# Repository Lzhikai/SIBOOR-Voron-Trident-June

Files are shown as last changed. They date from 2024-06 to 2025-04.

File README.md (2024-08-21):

## To improve readability, the assembly and debugging guides for the Trident JUNE have been gradually migrated to [https://docs.siboor.com/](https://docs.siboor.com/).

## The `printer.cfg` was updated on August 20:
1. Fixed the issue with excessively high maximum speed values.
2. Corrected the issue with excessively low maximum acceleration values.
3. Reversed the direction of the extruder motor.
4. Rewrote all fan configurations to allow separate activation and control of the FumePack filter module and additional part cooling fans in slicing.
5. Reduced the speed of the `z_tilt` operation.
6. Rewrote the macros for starting and ending prints.
7. Removed the Cartographer model to prevent users from homing without calibrating Cartographer.

# SIBOOR-Voron-Trident-June  

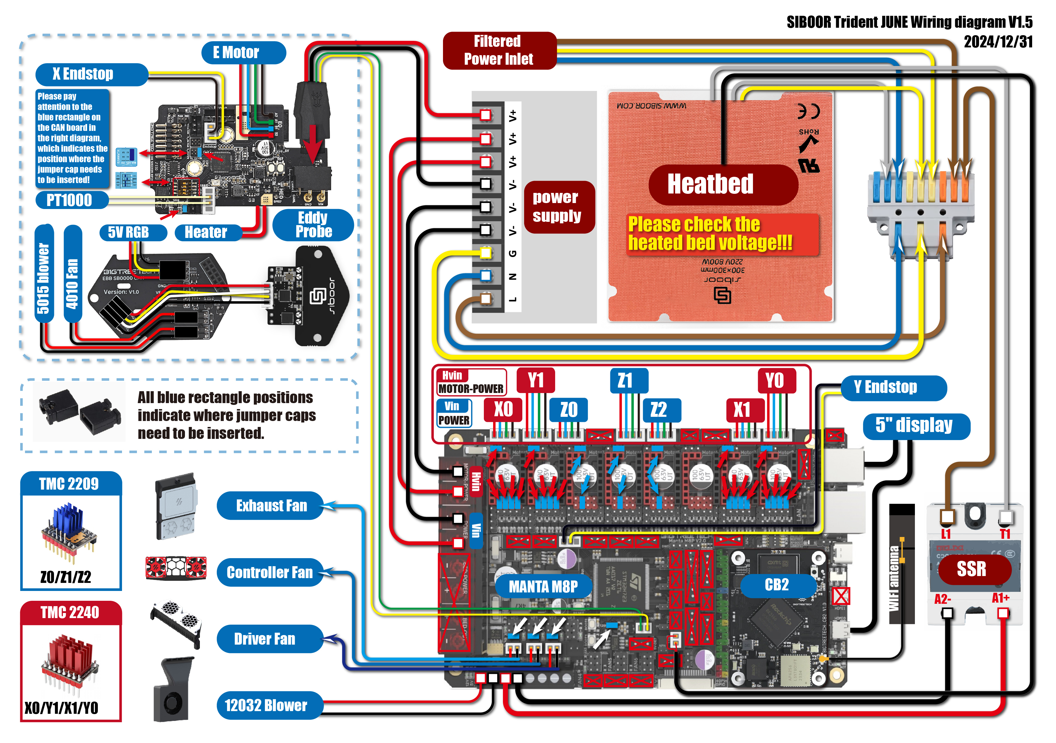
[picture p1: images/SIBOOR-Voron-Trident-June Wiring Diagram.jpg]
  

### SIBOOR-Voron-Trident-June  [BOM](https://github.com/Lzhikai/SIBOOR-Voron-Trident-June/blob/main/SIBOOR_Trident_%5BJUNE_2024%5D_BOM.md)
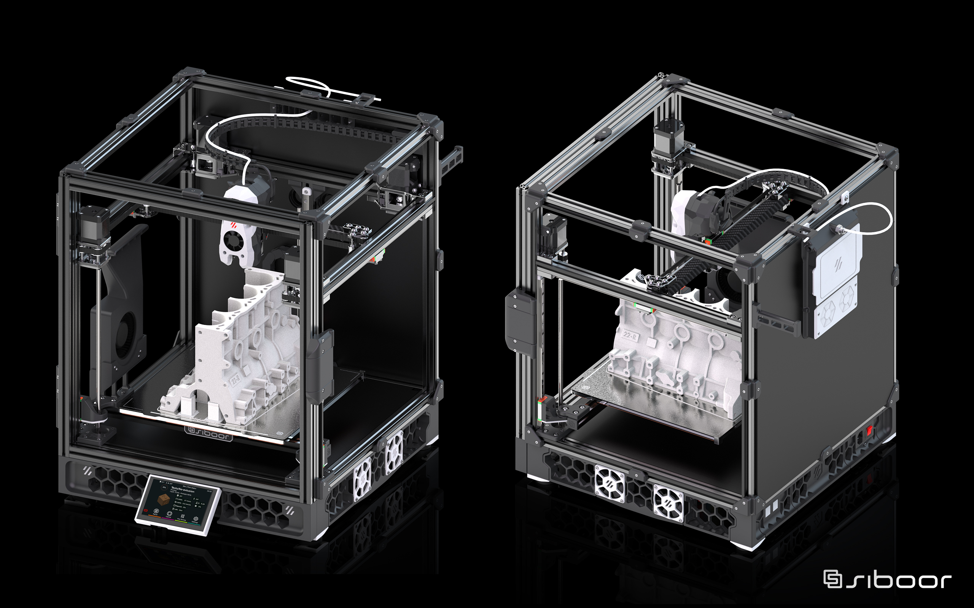
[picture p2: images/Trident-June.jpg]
  
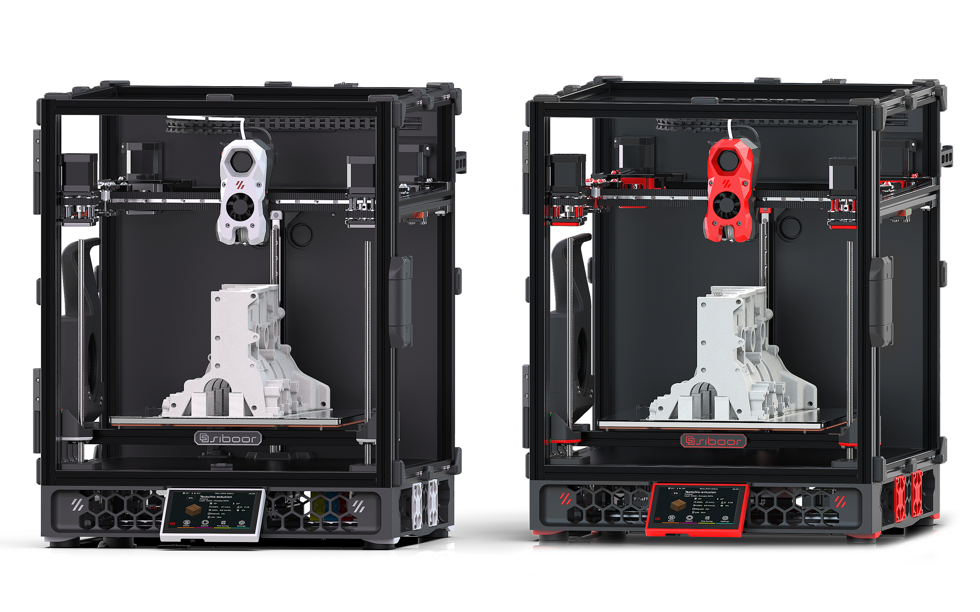
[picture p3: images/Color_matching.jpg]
  
# <p align="center"> 《CNC AWD metal parts schematic diagram》</p>    
  
<p align="center" >
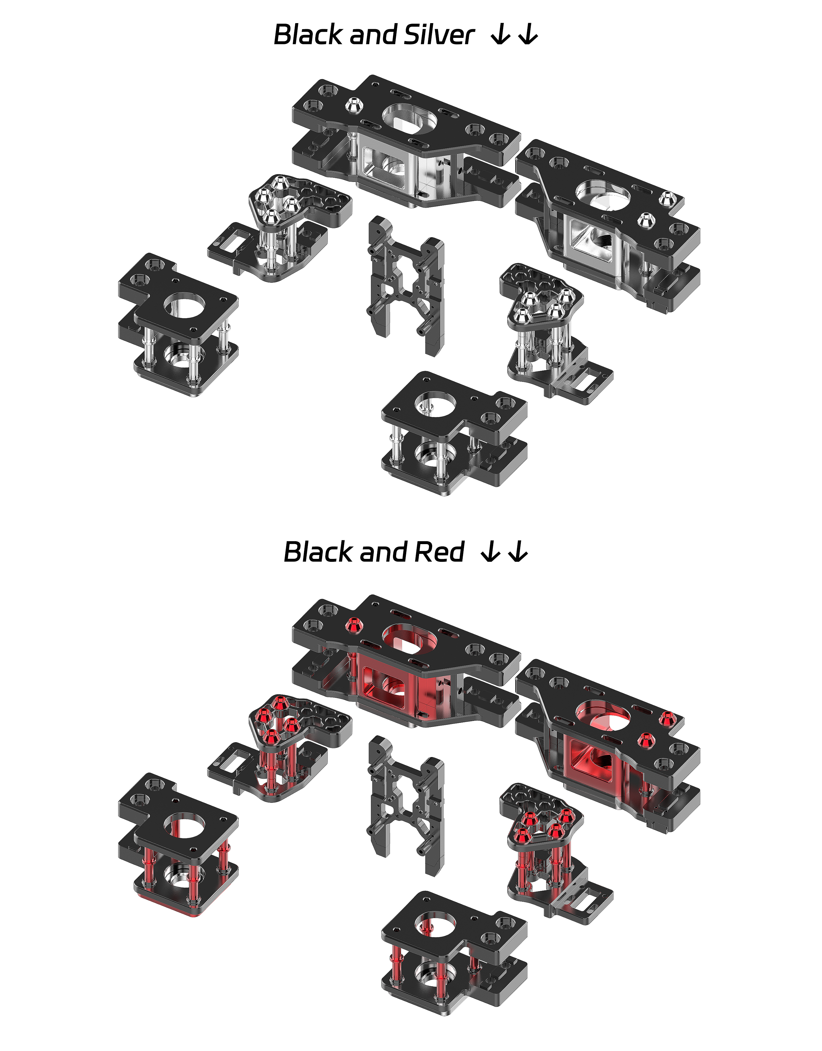
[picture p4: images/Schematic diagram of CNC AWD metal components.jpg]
    
</p>

# <p align="center">ABS essential functional parts  </p>    
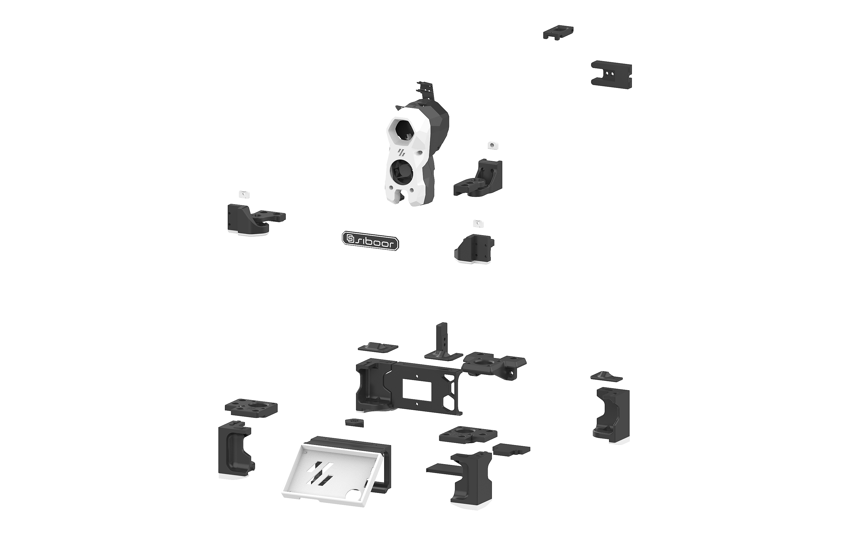
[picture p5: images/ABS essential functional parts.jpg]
  
# <p align="center">Other than the necessary functional parts of ABS  </p>    
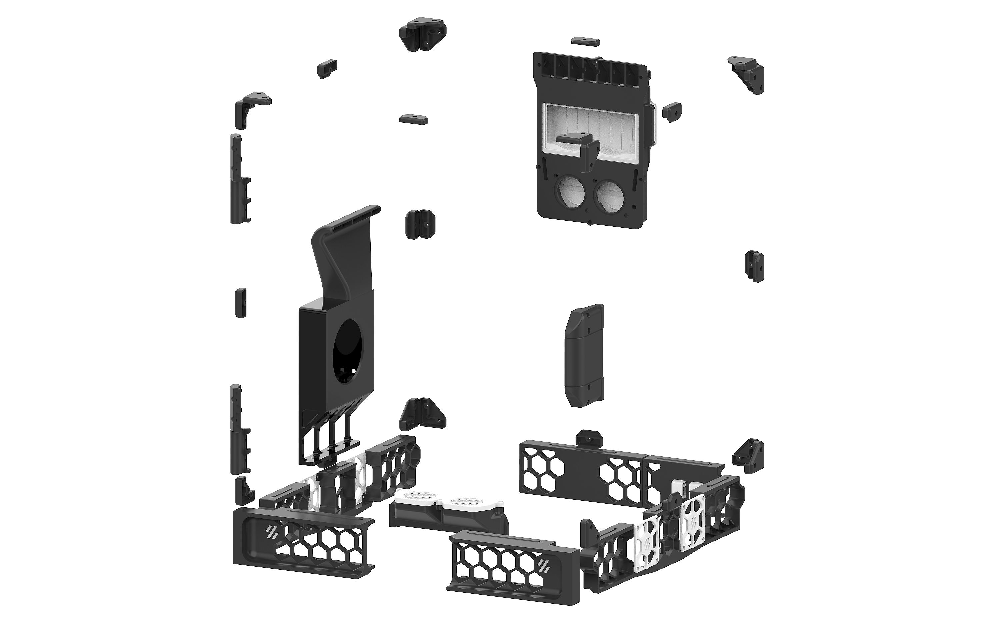
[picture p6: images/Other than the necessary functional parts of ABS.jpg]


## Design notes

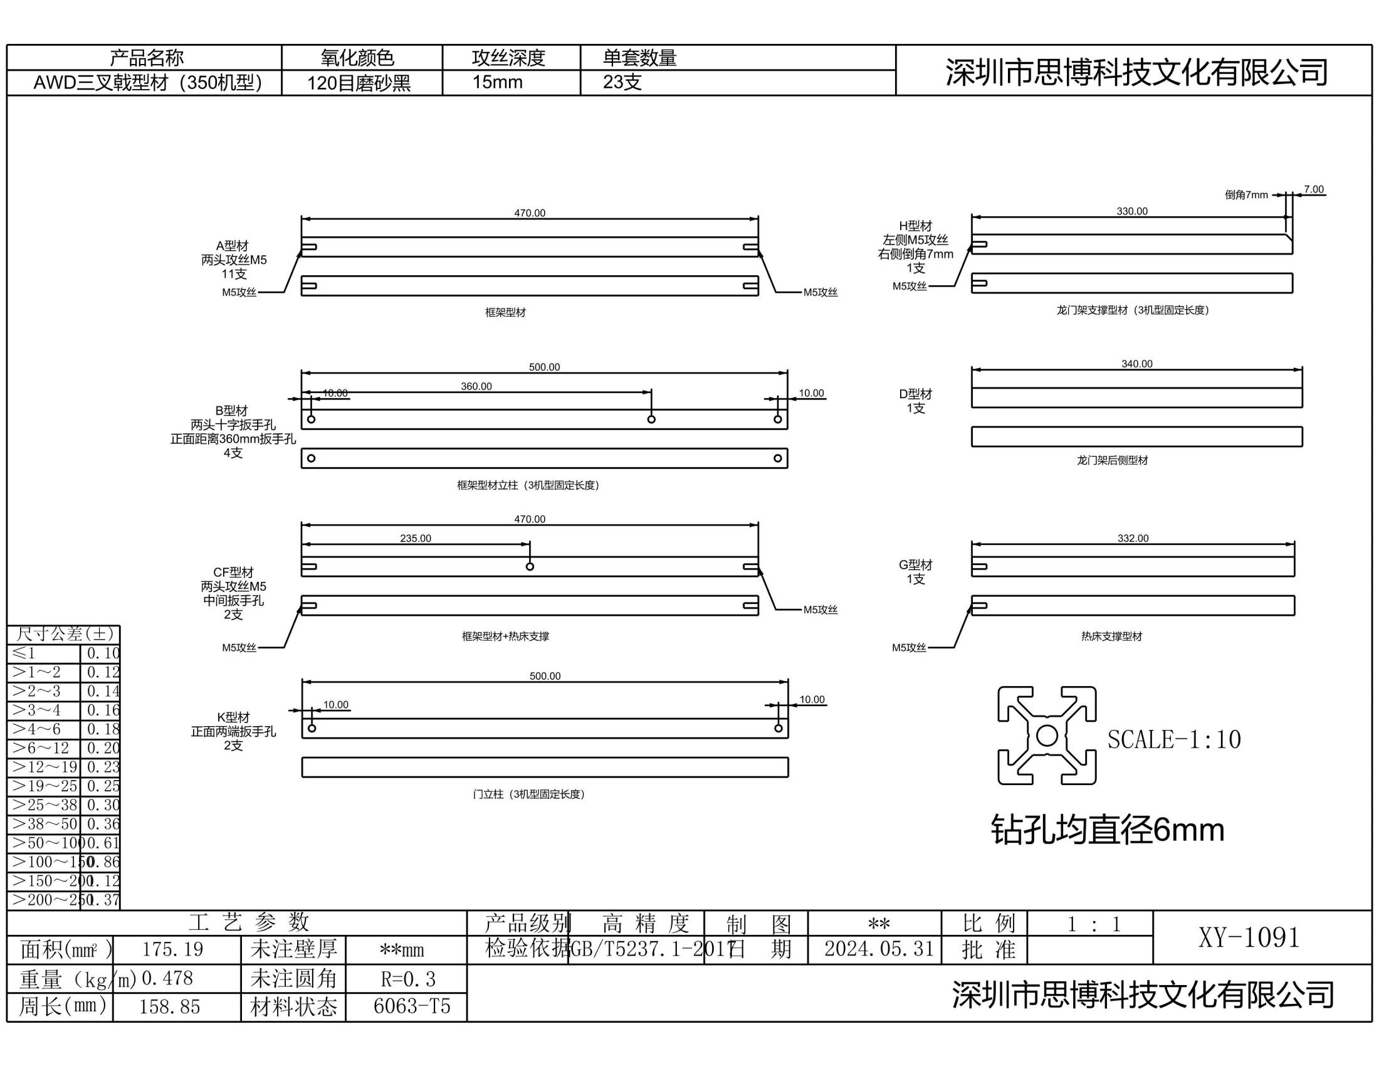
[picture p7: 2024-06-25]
Standard book/Extrusion/Trident_350_model_extrusion.jpg

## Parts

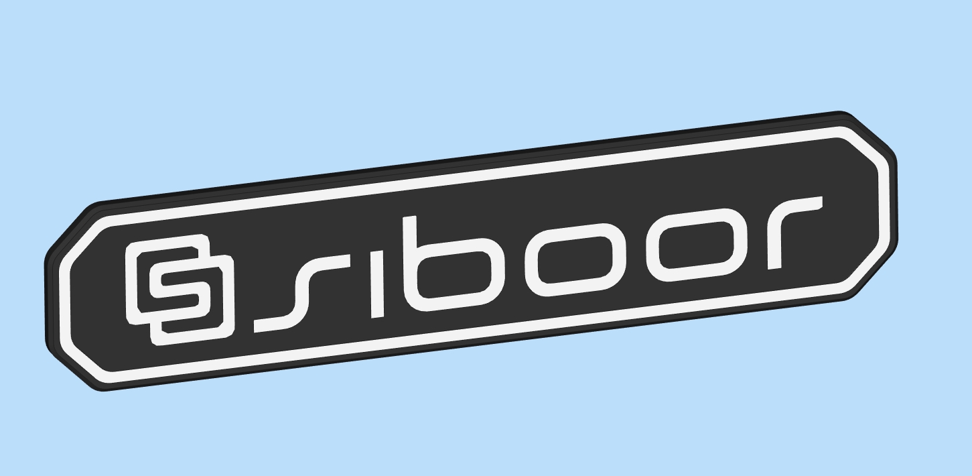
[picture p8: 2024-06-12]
STL/SIBOOR_Trident_[JUNE]_Essential__Functional_Parts/Other/Refer to Figure 2.png

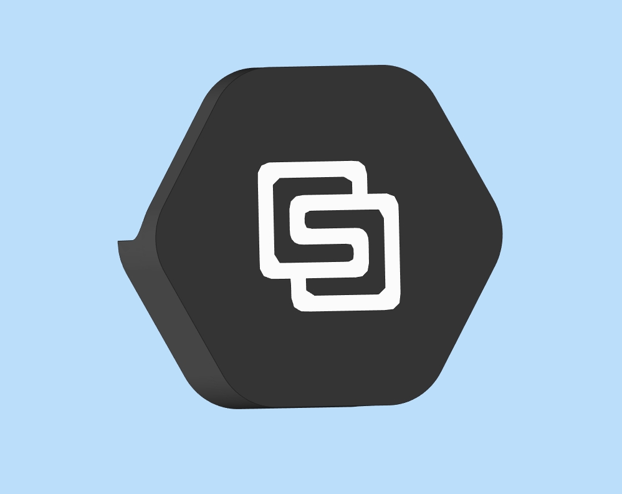
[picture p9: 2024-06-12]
STL/SIBOOR_Trident_[JUNE]_Essential__Functional_Parts/Other/Refer to Figure 1.png

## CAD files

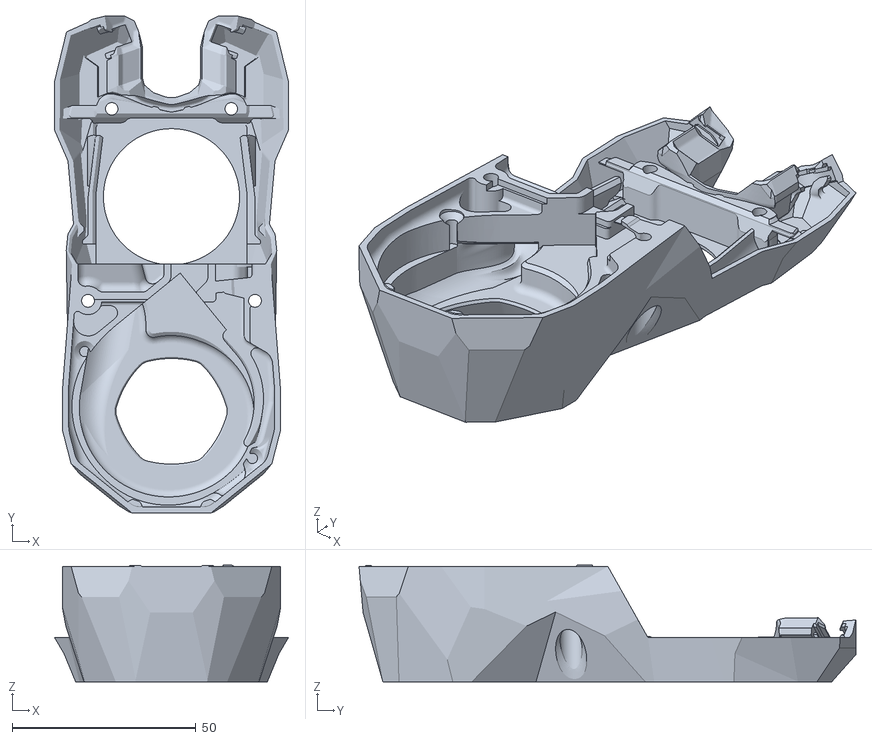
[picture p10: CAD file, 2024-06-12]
STL/SIBOOR_Trident_[JUNE]_Essential__Functional_Parts/Stealthburner/[a]_stealthburner UHF_main_body.stl
63.6 x 135.1 x 31.8

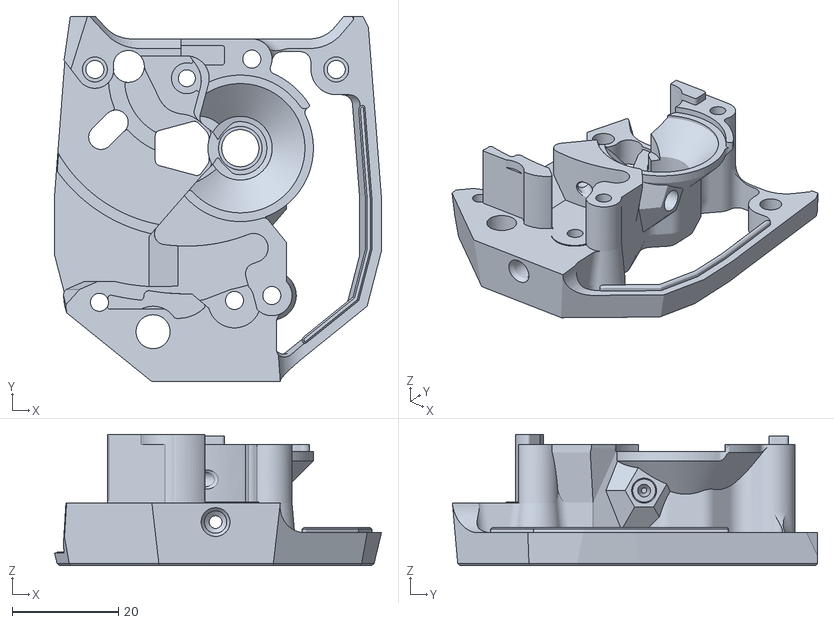
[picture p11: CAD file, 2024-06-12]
STL/SIBOOR_Trident_[JUNE]_Essential__Functional_Parts/Stealthburner/main_body_by_SIBOOR.stl
61.5 x 68.7 x 24.7

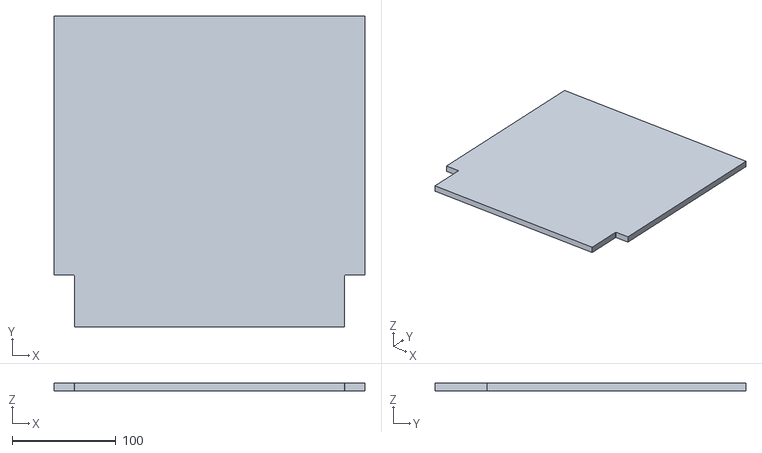
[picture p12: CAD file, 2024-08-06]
Configure/OrcaSlicer/300 Model/Trident_JUNE_300_Print_bed_Shape.stl
300.0 x 300.0 x 8.00

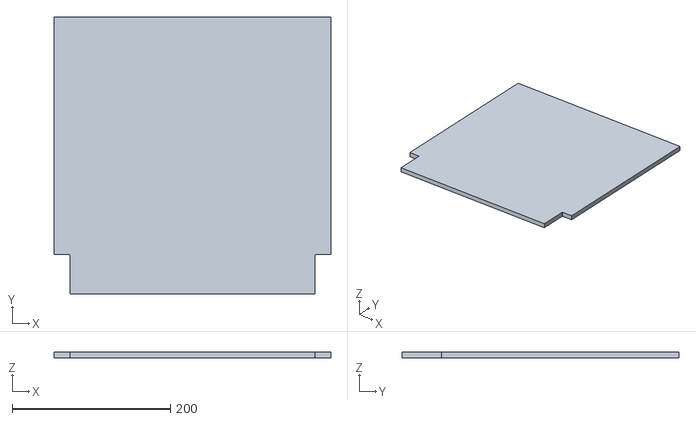
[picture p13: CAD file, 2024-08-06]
Configure/OrcaSlicer/350 Model/0806Trident_JUNE_350__bed_Shape.stl
350.0 x 350.0 x 8.00

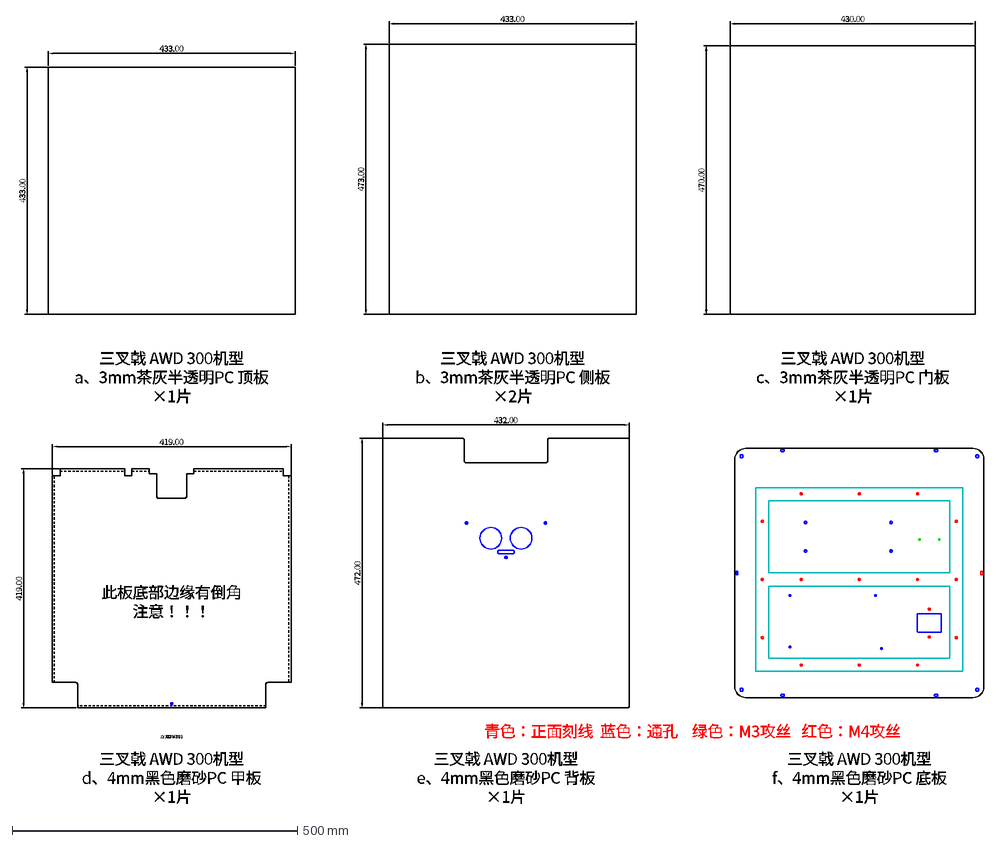
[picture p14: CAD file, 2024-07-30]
Panel/Trident_AWD_300_Model_PC_Panel_Drawing.dxf
470.00
430.00
473.00
433.00
此板底部边缘有倒角 注意！！！
472.00
419.00
432.00
底部需要倒斜角
三叉戟 AWD 300机型 f、4mm黑色磨砂PC 底板 ×1片
三叉戟 AWD 300机型 e、4mm黑色磨砂PC 背板 ×1片
三叉戟 AWD 300机型 d、4mm黑色磨砂PC 甲板 ×1片
三叉戟 AWD 300机型 c、3mm茶灰半透明PC 门板 ×1片
三叉戟 AWD 300机型 b、3mm茶灰半透明PC 侧板 ×2片
三叉戟 AWD 300机型 a、3mm茶灰半透明PC 顶板 ×1片
青色：正面刻线 蓝色：通孔 绿色：M3攻丝 红色：M4攻丝

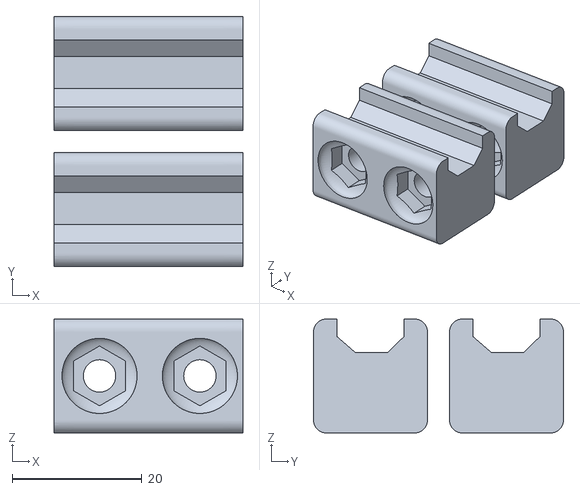
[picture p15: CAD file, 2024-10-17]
STL/SIBOOR_Trident_[JUNE]_Essential__Functional_Parts/Other/X Carbon Tube Fixings【FLANGE NUT】.stl
29.1 x 38.6 x 17.6

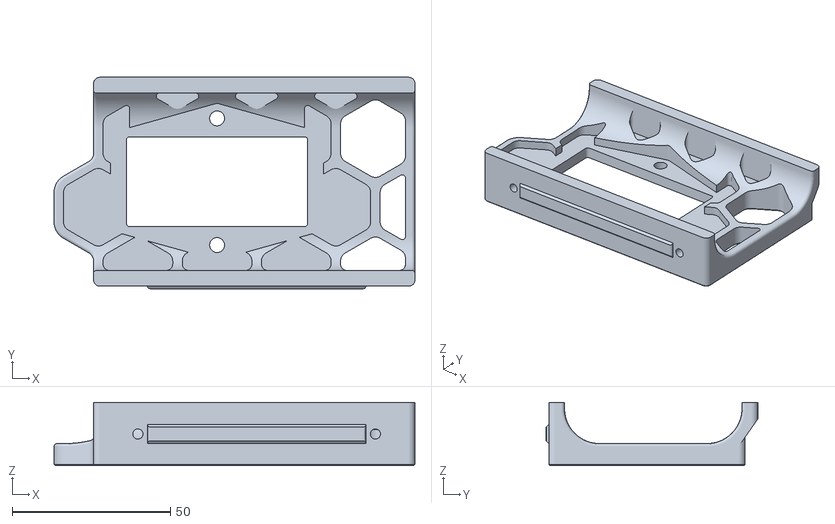
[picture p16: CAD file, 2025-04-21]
STL/SIBOOR_Trident_[JUNE]_Essential__Functional_Parts/Skirt/56mm-0708power_inlet_adamstech_by_SIBOOR.stl
114.0 x 66.8 x 20.0

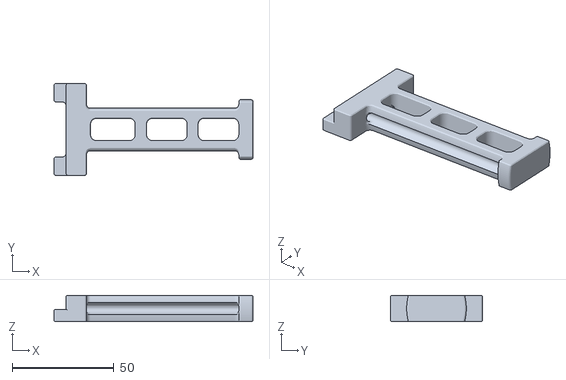
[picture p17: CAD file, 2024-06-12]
STL/SIBOOR_Trident_[JUNE]_Essential__Functional_Parts/Spool_Management/spool_holder.stl
98.0 x 45.4 x 13.0

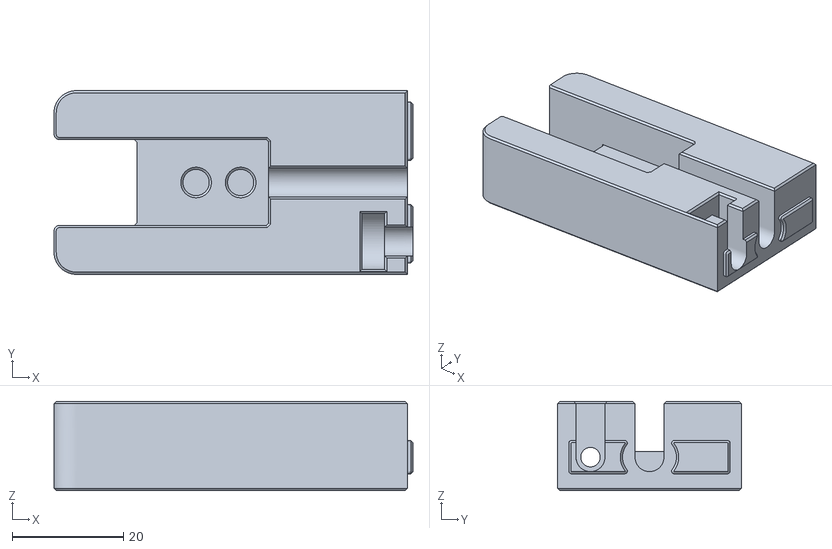
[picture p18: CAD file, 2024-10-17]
STL/SIBOOR_Trident_[JUNE]_Essential__Functional_Parts/Stealthburner/Distal_end_of_drag_chain bracket_by_SIBOOR.stl
64.5 x 33.0 x 16.0

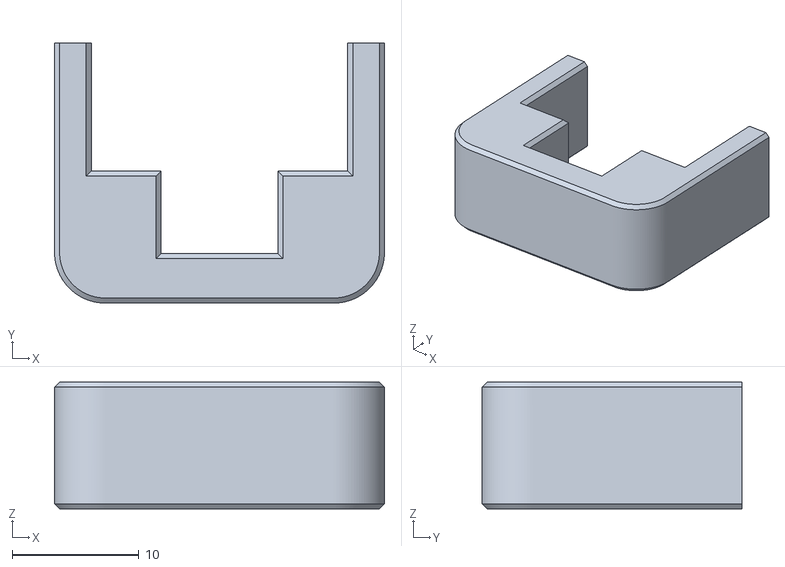
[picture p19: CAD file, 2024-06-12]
STL/SIBOOR_Trident_[JUNE]_Essential__Functional_Parts/Tools/MGN9_rail_guide_x2.stl
26.0 x 20.5 x 10.0

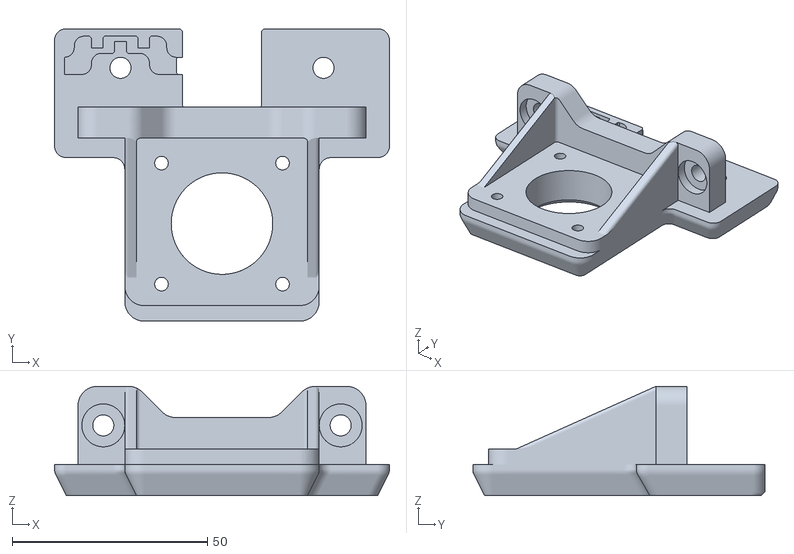
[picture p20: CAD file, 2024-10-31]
STL/SIBOOR_Trident_[JUNE]_Essential__Functional_Parts/Z_Assembly/z_stepper_rear_by_SIBOOR.stl
85.8 x 74.9 x 28.0

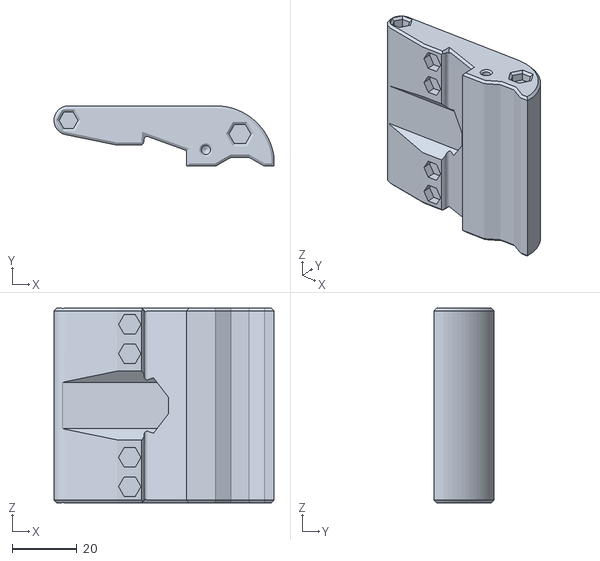
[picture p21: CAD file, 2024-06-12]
STL/SIBOOR_Trident_[JUNE]_Non-essential_Functional_Parts/clickyclacky_door/Handle.stl
67.9 x 18.6 x 60.0

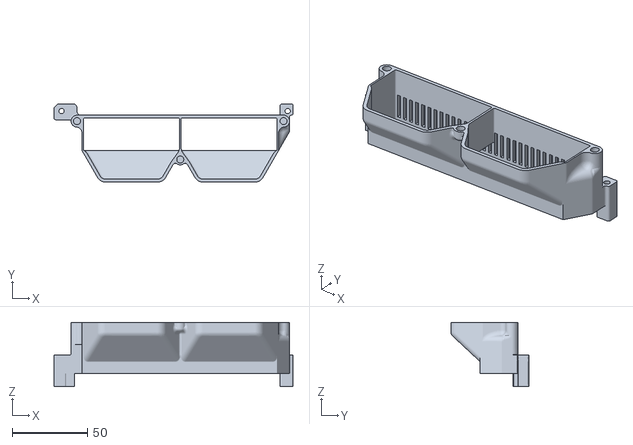
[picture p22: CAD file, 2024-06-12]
STL/SIBOOR_Trident_[JUNE]_Non-essential_Functional_Parts/MANTA M8P Thermal Module/M8P_Heat sink module body.stl
158.5 x 51.8 x 42.6

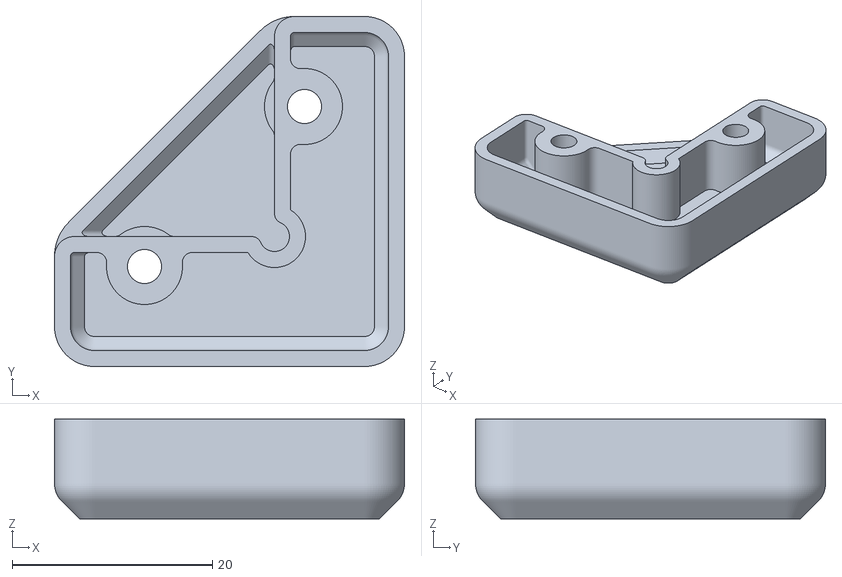
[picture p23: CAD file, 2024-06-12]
STL/SIBOOR_Trident_[JUNE]_Non-essential_Functional_Parts/Panels/corner_panel_clip_6mm_x8.stl
35.0 x 35.0 x 10.00

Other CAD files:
Standard book/Panel/SIBOOR_Trident_JUNE_350_model_panel.dwg
STL/SIBOOR_Trident_[JUNE]_Non-essential_Functional_Parts/Skirt/300/front_skirt_b_300_by_SIBOOR.stl
STL/SIBOOR_Trident_[JUNE]_Non-essential_Functional_Parts/Skirt/350/front_skirt_b_350_by_SIBOOR.stl
STL/SIBOOR_Trident_[JUNE]_Non-essential_Functional_Parts/Skirt/[a]_skirt_logo_x2.stl
Configure/OrcaSlicer/300 Model/Trident_JUNE_300_Printer_Bed_Model.stl
Configure/OrcaSlicer/350 Model/Trident_JUNE_350_Printer_Bed_Mould.stl
Panel/Trident_AWD_350_Model_PC_Panel_Drawing.dxf.dxf
STL/SIBOOR_Trident_[JUNE]_Essential__Functional_Parts/Other/Skirt Fan Adapter PCB Bracket.stl
STL/SIBOOR_Trident_[JUNE]_Essential__Functional_Parts/Other/[Two-color] Deck Handle_by_SIBOOR.stl
STL/SIBOOR_Trident_[JUNE]_Essential__Functional_Parts/Other/[Two-color] SIBOOR nameplate_by_SIBOOR.stl
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

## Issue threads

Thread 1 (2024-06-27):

The BOM for the 350 model is wrong

marcmontecalvo, 2024-06-27:
https://github.com/Lzhikai/SIBOOR-Voron-Trident-June/blob/main/SIBOOR_Trident_%5BJUNE_2024%5D_BOM.md
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
You can see that the Linear Rails and Timing Belt are all one line too high on the 350 model.  All other items appear to be in the correct spot though.

notavisitor, 2024-07-04:
Thanks. Fixed it.

notavisitor, 2024-07-04:
Thanks. Fixed it.

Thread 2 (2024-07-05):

Some improvements to the manual (or things I saw)

Dave811, 2024-07-05:
First thing, it seems so far well documented, and I can't wait to build it in August.

I am on the version of the document that was distributed on the discord (20240705 Assembly_Manual_SIBOOR_Trident_JUNE.pdf)

1. The Page numbering is until page 27 correct
2. Then the Page number 28 is not on the left side
3. Then the numbering is in reverse uneven left and even right (the first pages were the opposite)
4. Then after page 30 came the 41, this time again on the right side, which seems to be the right orientation but perhaps the wrong page number
5. page 48 is on the right side, which should be on the left side and be 38?
6. page 51 appears to be again correct on the right side
7. ---
8. on page 50 (which should be 40) is a text behind another text (see the attached screenshot)
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

Closed 2024-07-09.

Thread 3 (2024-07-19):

Definition error regarding fan pins

Km0107, 2024-07-19:
[fan]
pin=multi_pin:my_fan             # Fan pin

↓

[fan]
pin: multi_pin:my_fan             # Fan pin

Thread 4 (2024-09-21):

Remixing allowed ?

WaschBaer0395, 2024-09-21:
under what license is this repository ? is remixing of parts allowed ?
i reworked the 12032 fan housing to be stiffer and wobble as much as the original did, aswell as rounding off some corners that looked weird cause they where not rounded at all compared to most other areas
also scale is off, this is not including abs shrinkage compensation, i fixed that aswell scaling it by 0.6% up

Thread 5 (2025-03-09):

Attaching the HDMI screen

carneeki, 2025-03-09:
In the Skirts chapter, I think there might be an error in the assembly manual.

The instruction on page 95 calls for 2x M3x8 SHCS but these were not long enough to engage the thread on the screen, I swapped for 2x M3x10 SHCS and was able to get the screen installed without the screw bottoming out, and the underside of the cap screw is seated firmly on the mount with 0.3Nm of torque.

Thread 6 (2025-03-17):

Jumper setups differs

ariloulaleelay, 2025-03-17:
Driver voltage selection for Z axis differs on this two images.
Which one is correct?

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

ggg25, 2025-04-17:
In colored version, Z1 and Z2 are receiving **VBB** which is **Vin**, XY are receiving HV which is **Hvin**

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

**HV** equals any voltage you supply to **HV IN**
**VBB** equals any (as long as it's enough to power the board) voltage you supply to **DCIN**
You can choose which voltage is supplied to the stepper drivers by placing jumpers between two of the three pins between the driver socket and motor connector.

You have the following options:

supply **24V** to **DCIN** and nothing to **HV IN**:
**VBB** will be at **24V**
**HV** will not have any voltage at all

supply **12V** to **DCIN** and nothing to **HV IN**:
**VBB** will be at **12V**
**HV** will not have any voltage at all

supply **24V** to **DCIN** and **24V** to **HV IN**:
**VBB** will be at **24V**
**HV** will be at **24V** too, but not drawing from **DCIN**

supply **24V** to **DCIN** and **48V** to **HV IN**:
**VBB** will be at **24V**
**HV** will be at **48V**

This give you the option to use multiple power supplies to power the board and the motors. Or you can split the power between different rails on a single power supply (feed system from one rail, feed motors from other rail). And if you have steppers that require a different voltage than you want to supply to DCIN, for example if you wish to use 48V steppers, you can do that too.

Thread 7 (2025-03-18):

Diffuser mask printed in the wrong material.

LazaroFilm, 2025-03-18:
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
The Siboor parts (Left) have the mask printed in clear [c] instead of opaque [o]. https://github.com/VoronDesign/Voron-Stealthburner/tree/main/STLs/Stealthburner

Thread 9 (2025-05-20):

Inconsistent Fan Connections in Manual

dotrey, 2025-05-20:
Looking at https://github.com/Lzhikai/SIBOOR-Voron-Trident-June/blob/main/Manual/New-1231%20Assembly_Manual_SIBOOR_Trident_JUNE.pdf

On page 192 in the wiring overview, the fans are connected from left to right:
- Exhaust Fan at `FAN0`
- Controller Fan at `FAN1`
- Driver Fan at `FAN2`

On page 197 where only the fan wiring is shown, the position of Controller Fan and Exhaust Fan are swapped:
- Controller at `FAN0`
- Exhaust at `FAN1`
- Driver at `FAN2`

When you follow the instructions on page 197, this will cause confusion with the default printer configuration, because the default `printer.cfg` uses `PF7` (=`FAN0`) for the Exhaust Fan and `PF9`(=`FAN1`) for the Controller Fan.

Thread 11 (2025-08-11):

Unknown pin chip name scanner

HRReaver, 2025-08-11:
Just finished SIboor Trident build.

Loaded CANBus UUIDs without issue.

When it boots,  the above error  causes Klipper to stop.

I followed 2 step troubleshooting guide.  Reordered config file and checked capitalization.  (This actually doesn't make since to me since config file is from Siboor.  So, it seems like it shouldn't have errors like this.)

I cannot check symlinks or reload cartographer since klipper is stopped.

Not sure what to do next.

If you had this problem, how did you fix?

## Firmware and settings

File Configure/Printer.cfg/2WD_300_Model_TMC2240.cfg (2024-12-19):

[include mainsail.cfg]                  # Include configuration from mainsail.cfg file

[virtual_sdcard]
path: /home/biqu/printer_data/gcodes    # Path to the virtual SD card directory
on_error_gcode: CANCEL_PRINT            # G-code to execute on error (defined in CANCEL_PRINT macro)

[gcode_arcs]
resolution: 0.1                         # Arc interpolation resolution, handles G2/G3 commands

[exclude_object]                        # Exclude object for cancellation

[force_move]
enable_force_move: true                 # Enable force move feature

#####################################################################
##	                 EBB SB2209(RP2040) Config
#####################################################################
[mcu EBBCan]
canbus_uuid: 2733cea0ce24              # Unique identifier for the CAN bus interface
# Acceleration sensor on cartographer sensor is recommended, 
# so the configuration of EBB is commented
#[adxl345]
#cs_pin: EBBCan:gpio1                   # Chip select pin
#spi_software_sclk_pin: EBBCan:gpio2    # SPI clock pin
#spi_software_mosi_pin: EBBCan:gpio0    # SPI master out slave in pin
#spi_software_miso_pin: EBBCan:gpio3    # SPI master in slave out pin
#axes_map: z,-y,x                       # Axis mapping settings
##SHAPER_CALIBRATE

#[resonance_tester]                     # Resonance tester configuration
#probe_points: 150, 150, 20             # Probe point positions
#accel_chip: adxl345                    # Acceleration chip used

[mcu]                                   # Main MCU configuration
#serial: /dev/serial/by-id/usb-Klipper_stm32h723xx_slipper-if00  # Serial port setting, this line is commented out
canbus_uuid: 41cbab4642d7               # CAN bus UUID
canbus_interface: can0                  # CAN bus interface

#####################################################################
##	                 Temperature Monitoring
#####################################################################
[temperature_sensor EBB_NTC]            # EBB_NTC temperature sensor configuration
sensor_type: Generic 3950               # Sensor type
sensor_pin: EBBCan:gpio28               # Sensor pin

[temperature_sensor BTT-MCU]            # BTT-MCU temperature sensor configuration       
sensor_type: temperature_mcu            # Sensor type

[temperature_sensor SOC]                # BTT-PI temperature sensor configuration
sensor_type: temperature_host           # Sensor type

#####################################################################
##                     Model and Acceleration
#####################################################################
[printer]                             # Printer configuration
kinematics: corexy                    # Printer type: corexy
max_velocity: 600                     # Maximum velocity (max 300)
max_accel: 10000                       # Maximum acceleration (max 4000)
max_z_velocity: 50                    # Maximum Z-axis velocity
max_z_accel: 100                      # Maximum Z-axis acceleration
minimum_cruise_ratio: 0.5             # Default 0.5
square_corner_velocity: 25            # Square corner velocity

#####################################################################
##                            X Axis
#####################################################################

[stepper_x]
step_pin: PE6                         # X-axis motor pulse pin setting
dir_pin: !PE5                         # X-axis motor direction pin setting
enable_pin: !PC14                     # X-axis motor enable pin setting
microsteps: 32                        # Motor microsteps setting
rotation_distance: 40                 # Active pulley circumference mm (2GT-20T pulley 40, 2GT-16T pulley 32)
full_steps_per_rotation: 200          # Number of pulses required for a single motor revolution (1.8 degree motor: 200, 0.9 degree motor: 400)
endstop_pin: EBBCan:gpio24            # Limit switch PIN setting (X-)
position_min: 0                       # X-axis minimum travel - software limit
position_endstop: 300                 # Mechanical reset point coordinates for X-axis
position_max: 300                     # X-axis maximum travel - software limit
homing_speed: 150                     # Homing speed maximum 100
homing_retract_dist: 5                # Setback distance after the first trigger of the homing switch
homing_positive_dir: true             # Direction of homing (generally no change required)

[tmc2240 stepper_x]
cs_pin: PC13                          # Chip select pin
spi_software_sclk_pin: PG8            # SPI clock pin
spi_software_mosi_pin: PG6            # SPI master out slave in pin
spi_software_miso_pin: PG7            # SPI master in slave out pin
driver_TPFD: 0                        # Driver setting
run_current: 1.5                      # Running current
interpolate: True                     # Interpolation


#####################################################################
##                           Y Aixs
#####################################################################

[stepper_y]
step_pin: PC7                         # Y-axis motor pulse pin setting
dir_pin: !PC8                         # Y-axis motor direction pin setting
enable_pin: !PD2                      # Y-axis motor enable pin setting
microsteps: 32                        # Motor microsteps setting
rotation_distance: 40                 # Active pulley circumference mm (2GT-20T pulley 40, 2GT-16T pulley 32)
full_steps_per_rotation: 200          # Number of pulses required for a single motor revolution (1.8 degree motor: 200, 0.9 degree motor: 400)
endstop_pin: PF2                      # Limit switch PIN setting (Y-)
position_min: 0                       # Y-axis minimum travel - software limit
position_endstop: 311.1               # Mechanical reset point coordinates for Y-axis (change to 350 for 350 models)
position_max: 311.1                   # Y-axis maximum travel - software limit (change to 350 for 350 models)
homing_speed: 150                     # Homing speed maximum 100
homing_retract_dist: 5                # Setback distance after the first trigger of the homing switch
homing_positive_dir: true             # Direction of homing (generally no change required)

[tmc2240 stepper_y]
cs_pin: PC6                           # Chip select pin
spi_software_sclk_pin: PG8            # SPI clock pin
spi_software_mosi_pin: PG6            # SPI master out slave in pin
spi_software_miso_pin: PG7            # SPI master in slave out pin
driver_TPFD: 0                        # Driver setting
run_current: 1.5                      # Running current
interpolate: True                     # Interpolation

#####################################################################
#    -------z1------- 
#   |                 |
#   |                 |
#   |                 |
#   |                 |
#   |                 |
#   |                 |
#  z0---   display ---z2
#####################################################################
##                  Z0 Axis
#####################################################################
[stepper_z]
step_pin: PB8                         # Z0-axis motor pulse pin setting
dir_pin: !PB7                         # Z0-axis motor direction pin setting
enable_pin: !PE0                      # Z0-axis motor enable pin setting
microsteps: 16                        # Motor microsteps setting
rotation_distance: 4                  # Active pulley circumference mm
endstop_pin: probe:z_virtual_endstop  # Limit switch PIN setting (Z0-)
position_max: 235                     # Z0-axis maximum travel - software limit
position_min: -5.0                    # Z0-axis minimum travel - software limit
homing_speed: 20                      # Homing speed
homing_retract_dist: 0                # Setback distance after the first trigger of the homing switch
homing_positive_dir: False            # Direction of homing (generally no change required)

#--------------------------------------------------------------------
[tmc2209 stepper_z]                   # TMC2209 driver settings
uart_pin: PB9                         # Driver communication port
interpolate: true                     # Enable 256 microstep interpolation
run_current: 0.8                      # Motor running current (mA)
hold_current: 0.8                     # Holding current (mA)

#--------------------------------------------------------------------
[stepper_z1]
step_pin: PB4                         # Z1-axis motor pulse pin setting
dir_pin: !PB3                         # Z1-axis motor direction pin setting
enable_pin: !PB6                      # Z1-axis motor enable pin setting
microsteps: 16                        # Motor microsteps setting
rotation_distance: 4                  # Active pulley circumference mm
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

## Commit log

2024-06-12 update STL
    [12032_Part_Fan_Cover.stl, 12032_Part_Fan_Duct.stl, 12032_Part_Fan_Housing.stl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]
2024-06-25 update STL STP
    [12032_Part_Fan_Housing.stl, HDMI5_Display_Bracket_by_SIBOOR.stl, SIBOOR_Trident_JUNE_300_model_panel.dwg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]
2024-07-02 Create SIBOOR-Voron-Trident-June Wiring Diagram.jpg
2024-07-03 Update SIBOOR-Voron-Trident-June Wiring Diagram.jpg
2024-07-17 Update Assembly_Manual_SIBOOR_Trident_JUNE .pdf
2024-07-18 update cfg
    [Trident_JUNE_300_Model_2240.cfg, Trident_JUNE_300_Model_5160.cfg, Trident_JUNE_350_Model_2240.cfg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]
2024-08-02 Update 0731 Assembly_Manual_SIBOOR_Trident_JUNE.pdf
2024-08-07 Create 0807 Assembly_Manual_SIBOOR_Trident_JUNE.pdf
2024-09-02 删除 delete
2024-10-04 power inlet
    [power_inlet_adamstech_by_SIBOOR .stl]
2024-12-19 300 model CAD
2025-04-21 power_inlet_adamstech_by_SIBOOR .stl
    [47mm-power_inlet_adamstech_by_SIBOOR .stl, 56mm-0708power_inlet_adamstech_by_SIBOOR.stl]
